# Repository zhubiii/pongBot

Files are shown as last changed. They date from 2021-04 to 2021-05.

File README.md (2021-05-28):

# pongBot
Progress on building a robot that can bounce a ping-pong ball forever...maybe more?

- [Methods](#Methods)
  - [Kinematics](#Kinematics)
  - [Theta offset](#Theta-offset)
  - [ROS](#ROS)
  - [Simulation](#Simulation)
    - [URDF](#URDF)
- [Build Progress](#Build-Progress)
  - [VERSION1](#VERSION1)
    - [Controller-Agent Unit](#Controller-Agent-Unit)
    - [Base](#Base)
    - [Link1](#Link-1)
    - [Link2](#Link-2)
    - [End-Effector](#End-Effector)
  - [VERSION2](#VERSION2)
- [Problems Encountered](#Problems-Encountered!)
- [TODO](#TODO)

# Methods
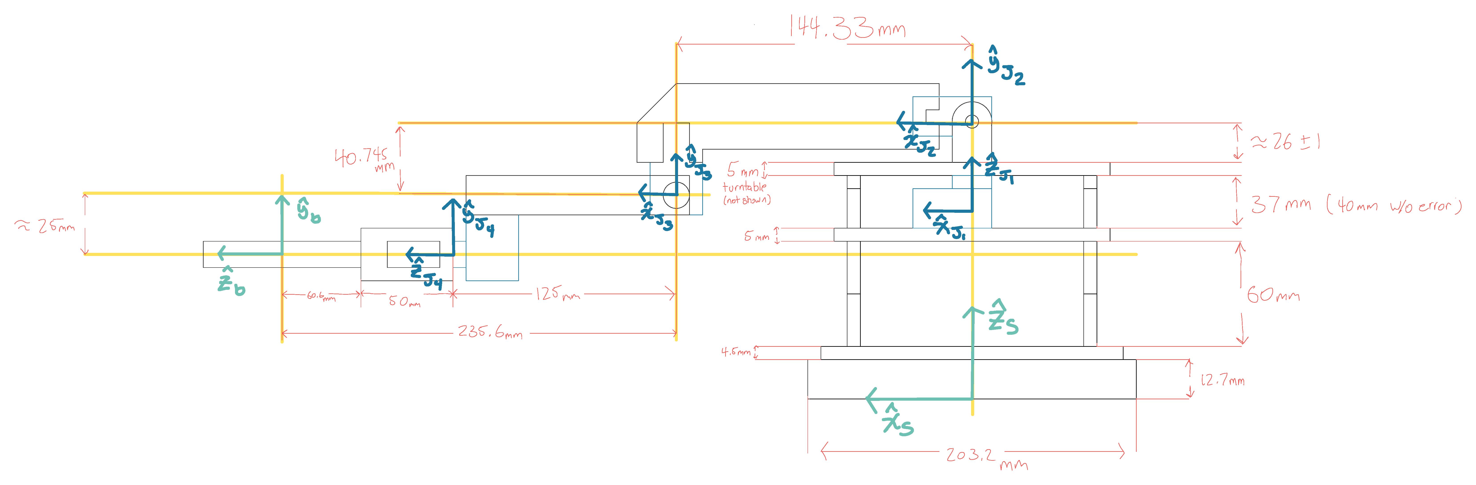
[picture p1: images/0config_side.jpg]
0config_side

## Kinematics
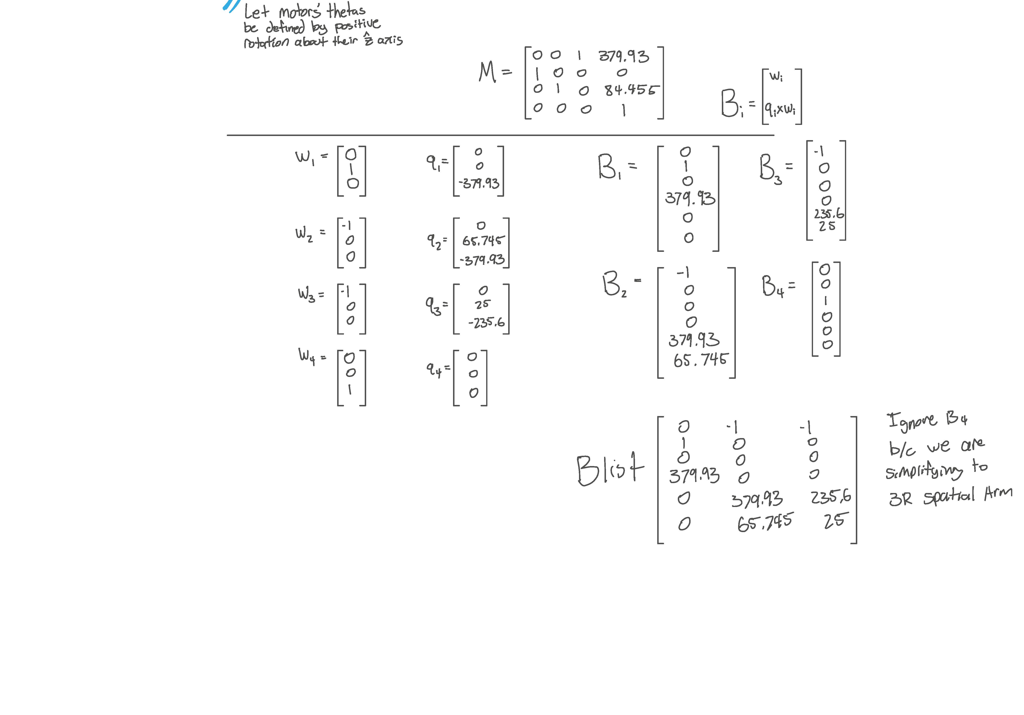
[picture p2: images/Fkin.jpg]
Fkin

## Theta offset
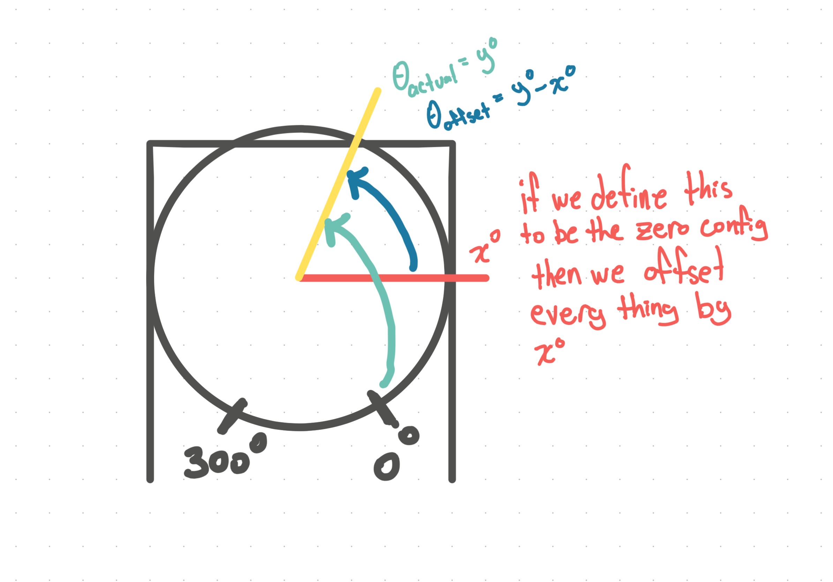
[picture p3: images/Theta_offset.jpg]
Theta offset

## ROS
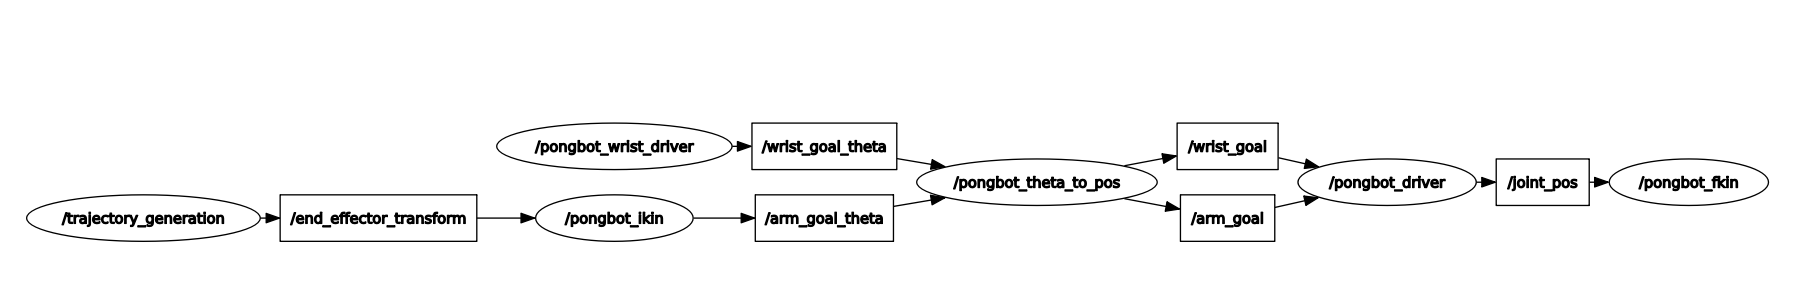
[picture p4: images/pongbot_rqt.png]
Rqt_graph


## Simulation

### URDF
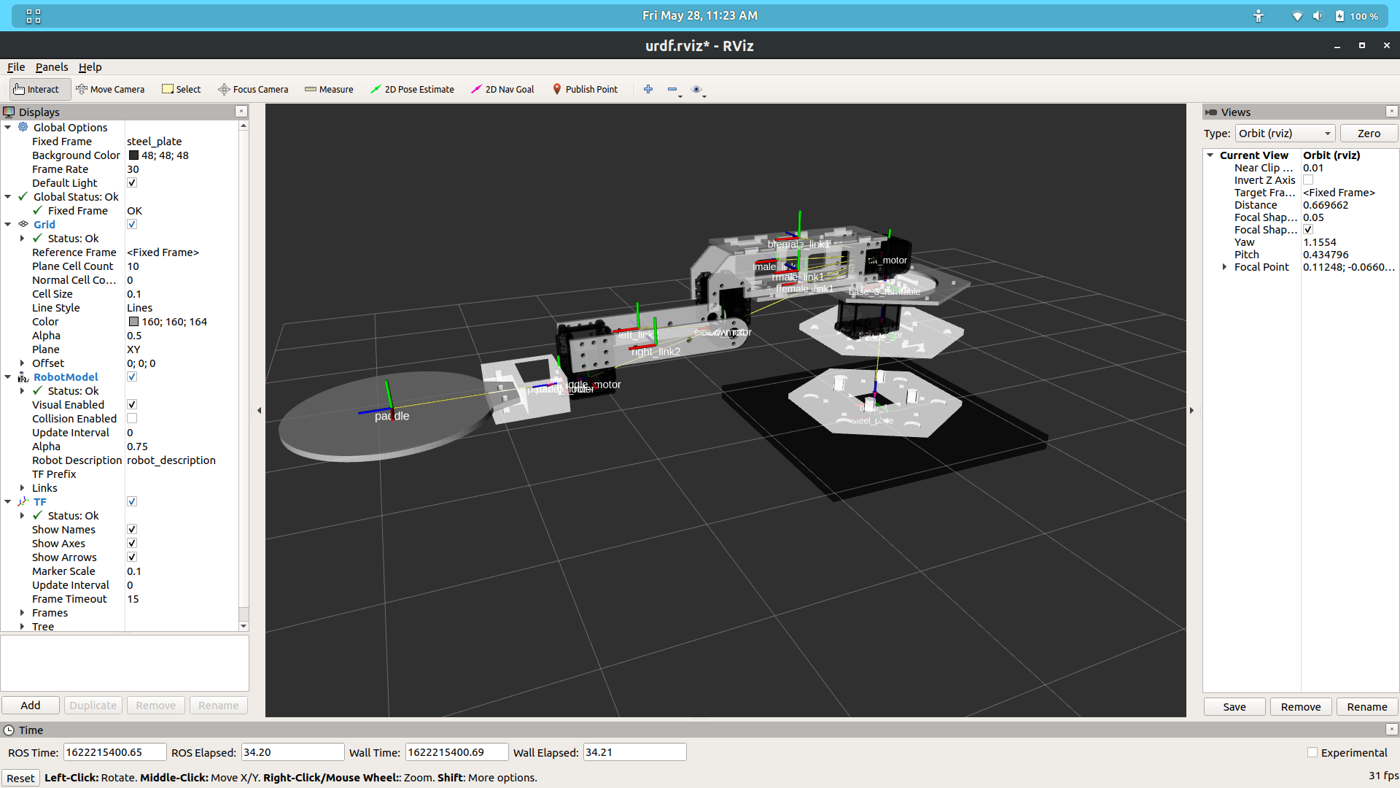
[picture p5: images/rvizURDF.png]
URDF in Rviz


# Build Progress
## VERSION1
### Controller-Agent Unit
- There are two of these units, one is the controller and one is the agent. The agent will always mimic the pan/tilt position of the controller   
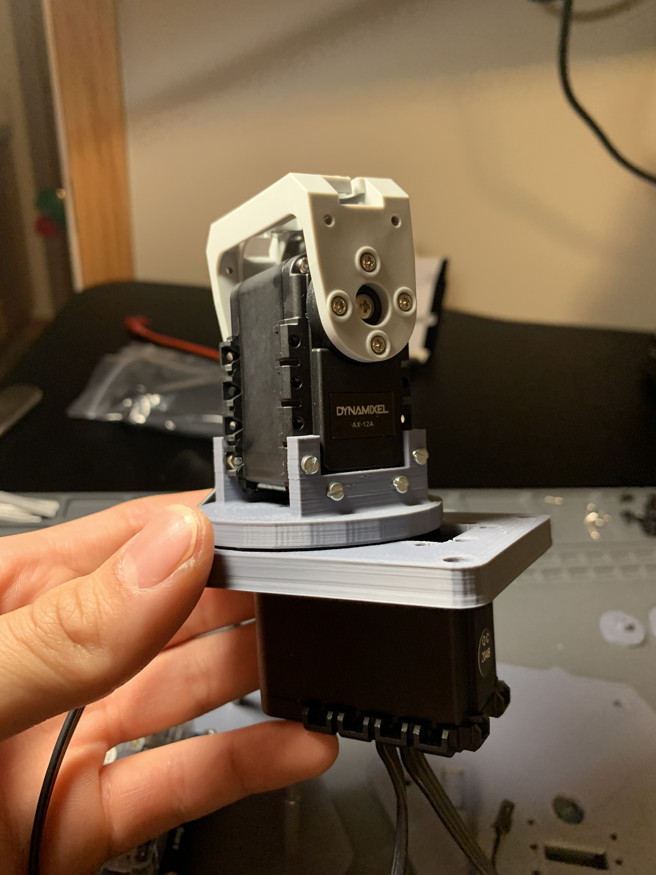
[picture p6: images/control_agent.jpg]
controller_agent


### Base
- There are 3 layers to the base
  - The first layer houses the U2D2 controller/PC interface
  - The second layer holds the pan motor which has the turntable attached to it and a spacer between for level
  - The third layer hodls the tilt motor which is a combination of the turntable and the rim
- Each of the layers are attached by standoffs
- I have plans to attach a steel plate to the bottom of the base such that the arm does not backflip off of a single rotation

. | . | .
:-:|:-:|:-:
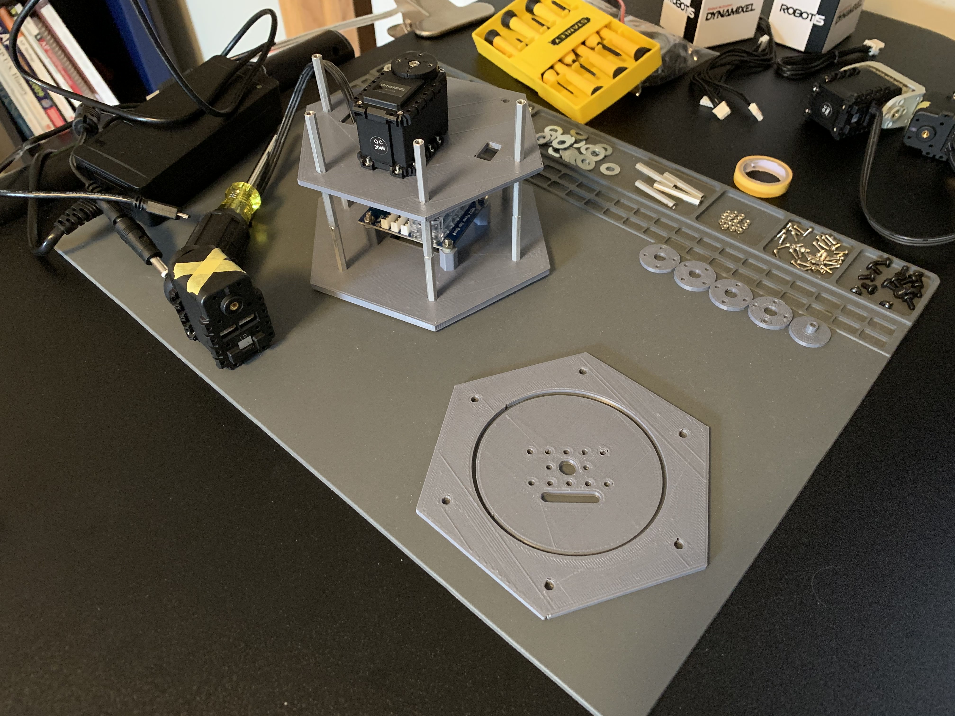
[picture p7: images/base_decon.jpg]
base deconstructed
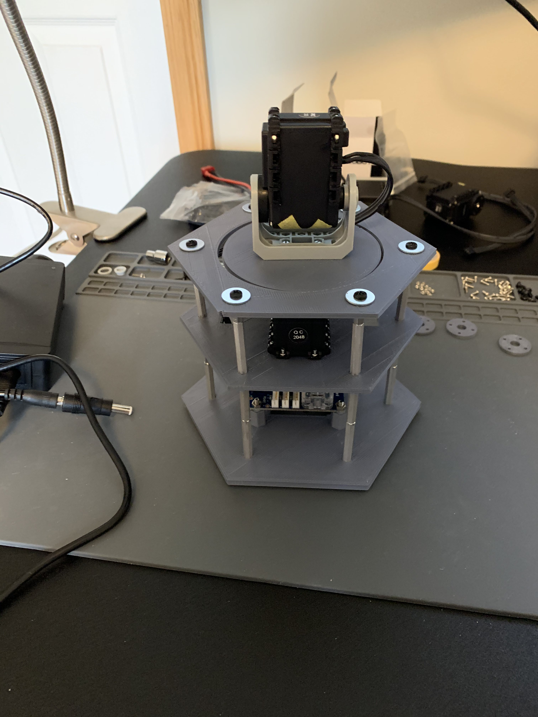
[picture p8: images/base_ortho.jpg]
base ortho view
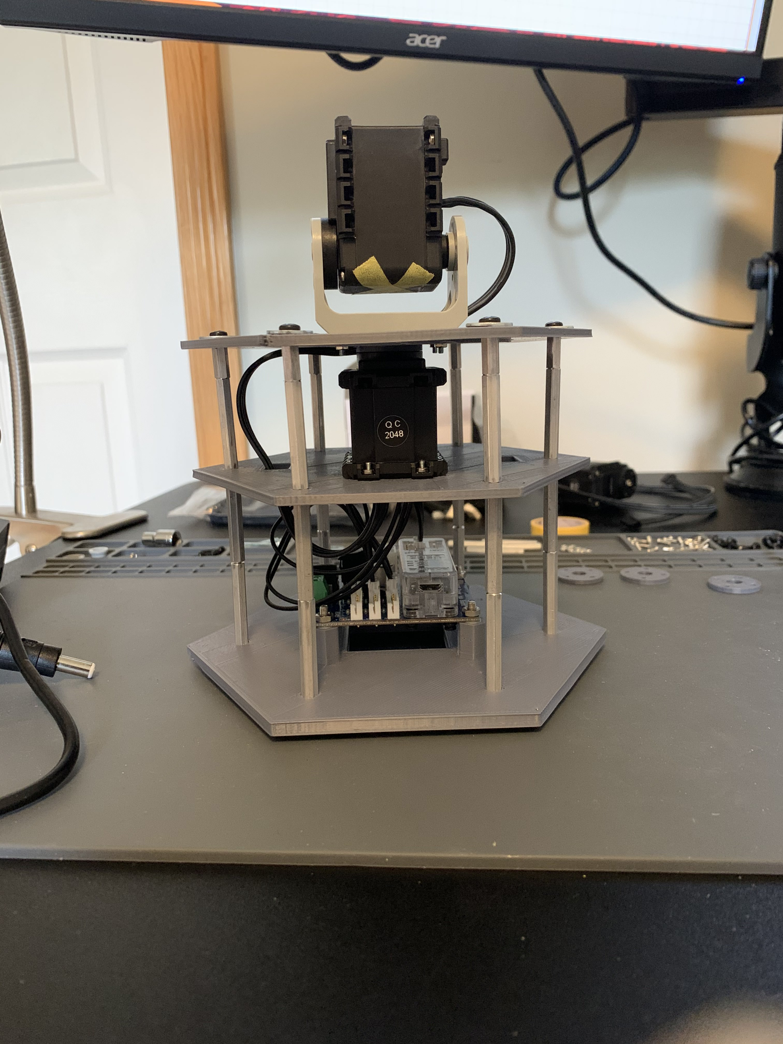
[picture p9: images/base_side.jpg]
base side view
||

### Link 1
- The first link is 4 plates that attach to the tilt motor. The front and back plates are linked by a standoff for support. The end of the link holds the second arm joint.

.|.|.|.
:-:|:-:|:-:|:-:
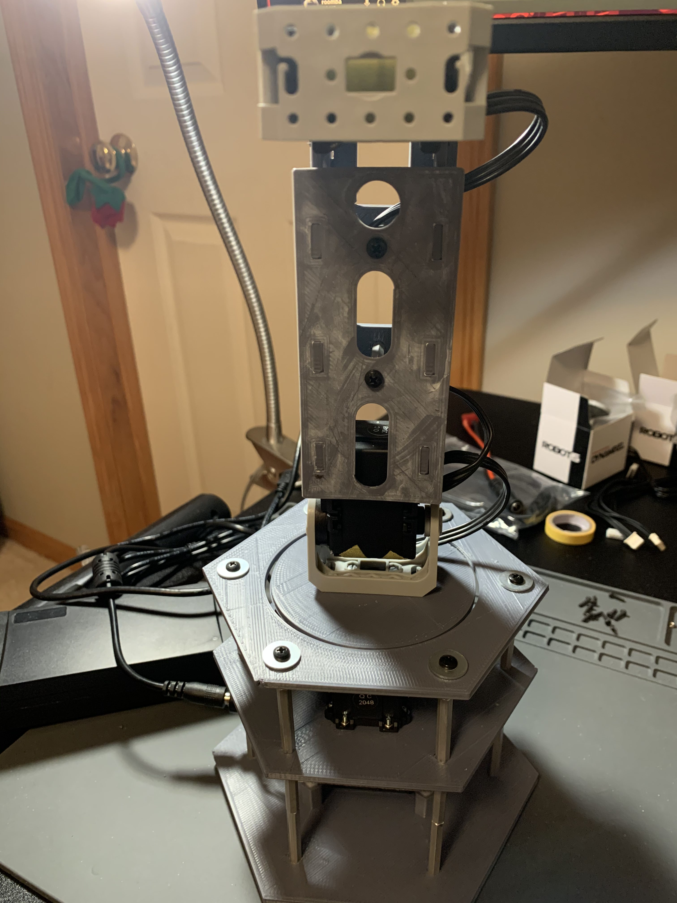
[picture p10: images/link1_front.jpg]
link1 front
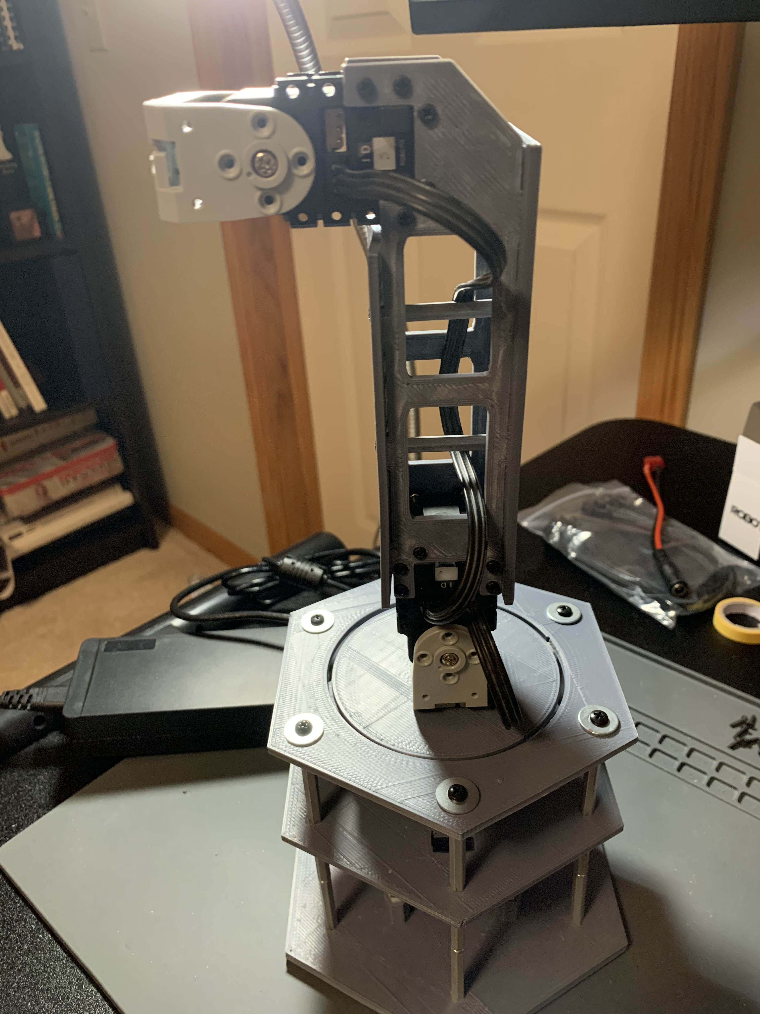
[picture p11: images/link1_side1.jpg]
link side1
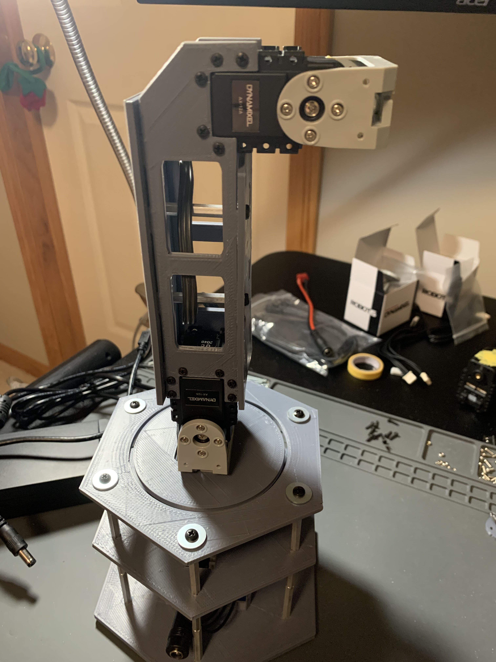
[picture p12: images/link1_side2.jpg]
link_side2
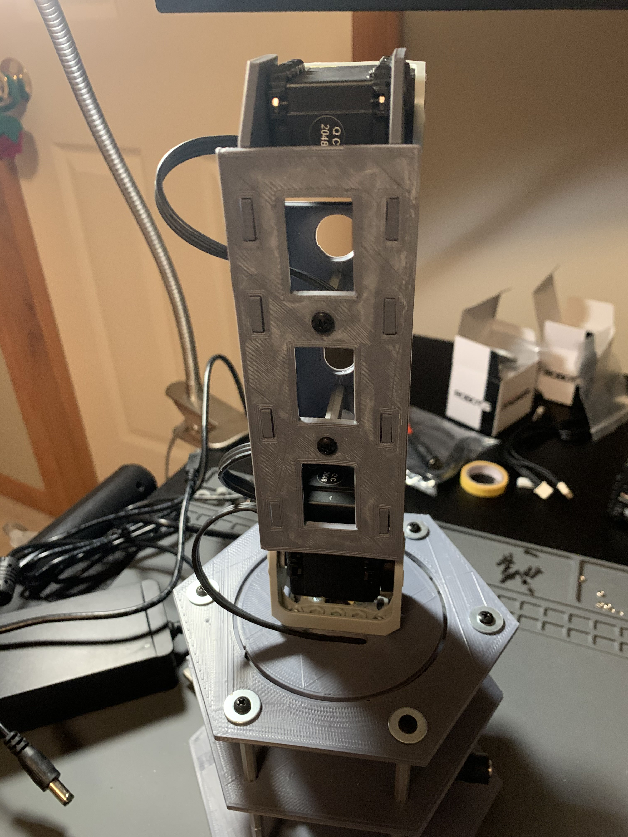
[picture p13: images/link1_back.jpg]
link_back
 |  |  | 

### Link 2
- The second link is a combination of 2 side panels joined by a standoff for support. The end of link2 holds the end effector

.|.|.|.
:-:|:-:|:-:|:-:
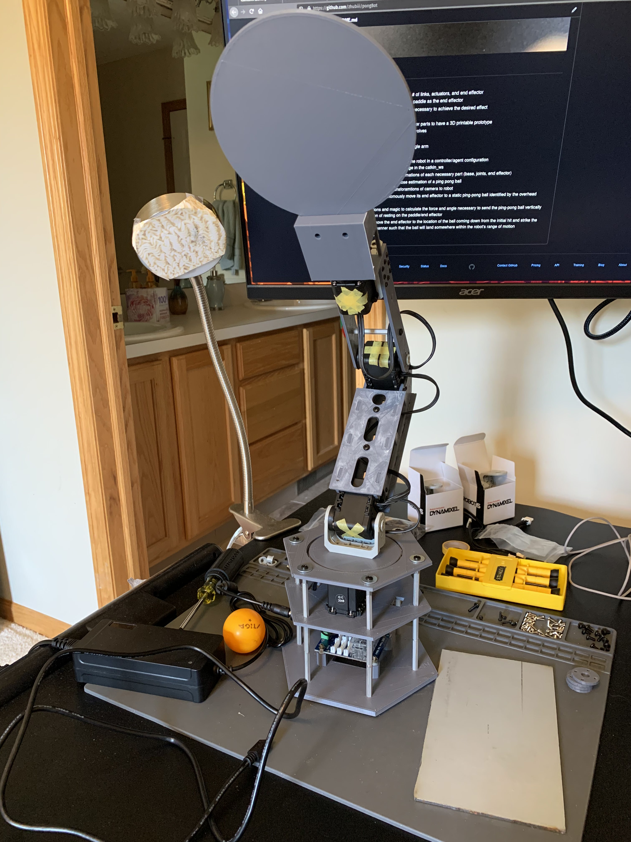
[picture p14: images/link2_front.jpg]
link2 front
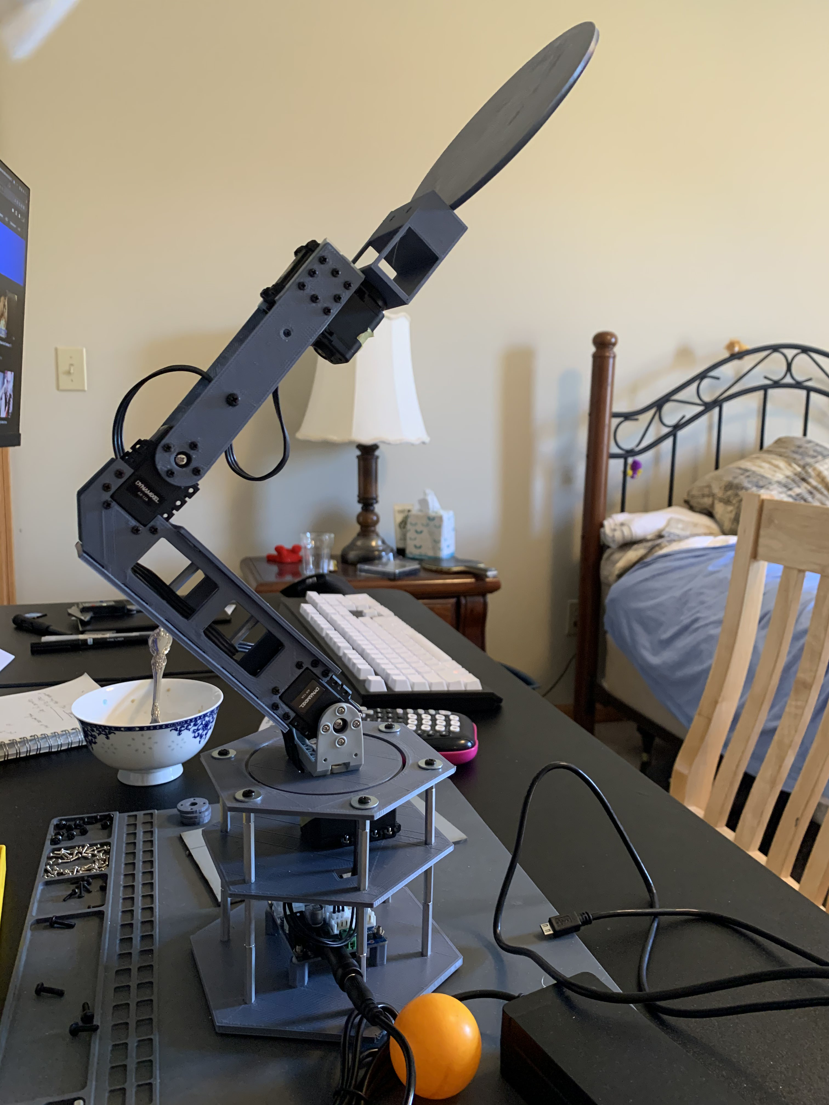
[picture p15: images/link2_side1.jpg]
link1 side1
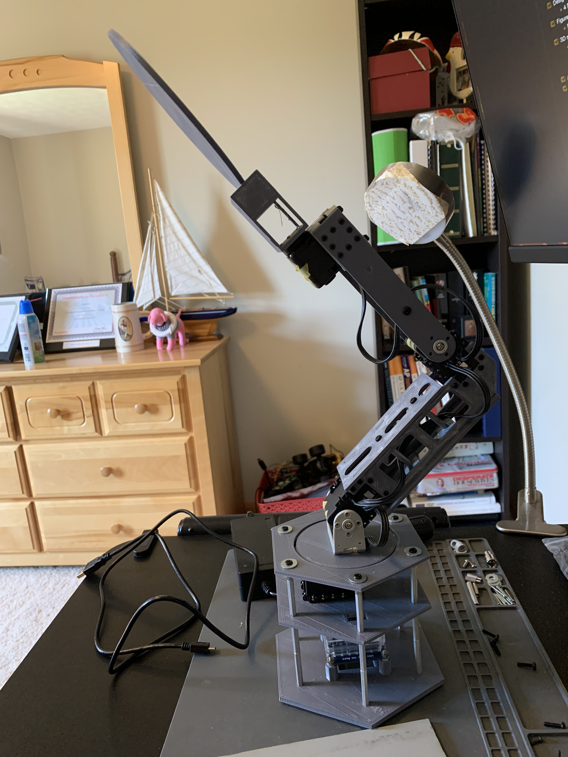
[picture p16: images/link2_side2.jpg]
link2_side2
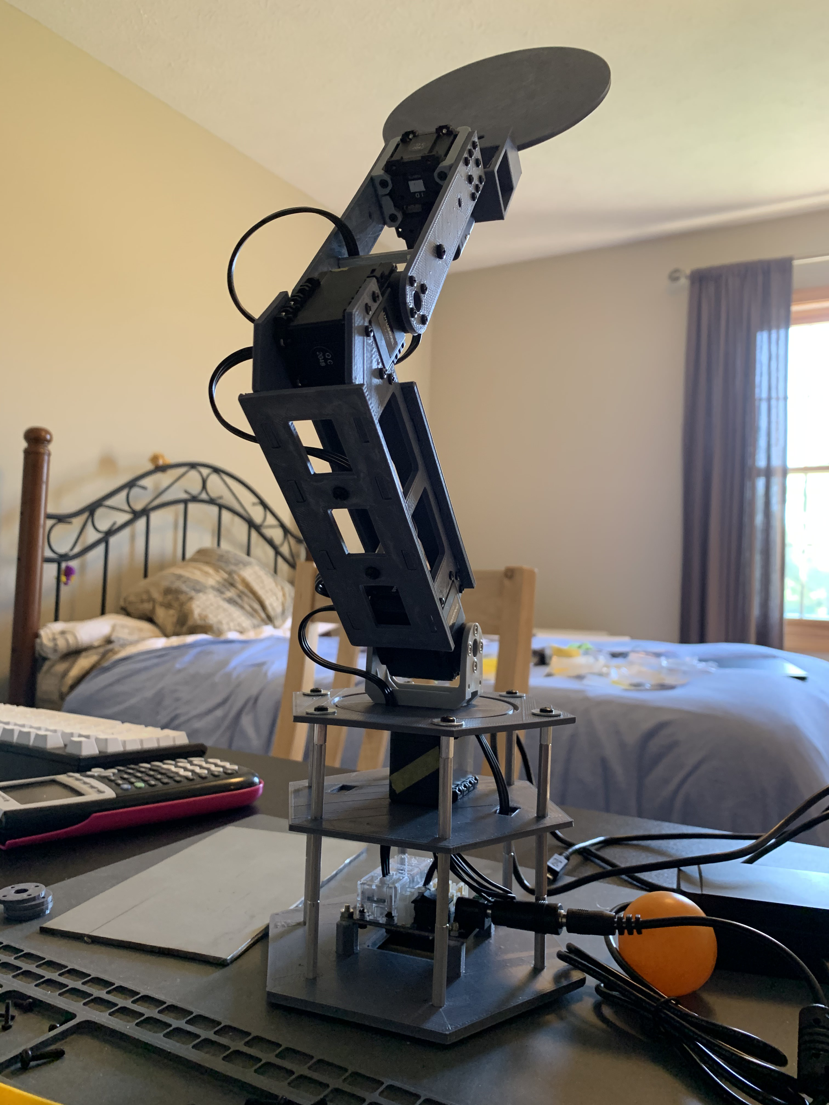
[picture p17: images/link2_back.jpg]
link_back
 |  |  | 

### End Effector
-  The end effector is a two piece 3-D printed paddle that attaches to a motor for angle control

## VERSION2
- The clear parts represents the reprints in PLA. I made them slightly thicker to reduce the wobble problem. In between the 
turntable and base2, I also put support beams. These were intended to have ball bearings on top but frankly I did not have
any on me at the time. I discovered, however, that the plastics are smooth enough to support and slide with minimal frictional resistance
- Lastly I was able to get a half-inch thick steel plate (thanks dad) to bolt the arm's base to. I drilled and tapped holes into it so 
now the arm will not do backflips everytime I attempt to move the end-effector

.|.
:-:|:-:
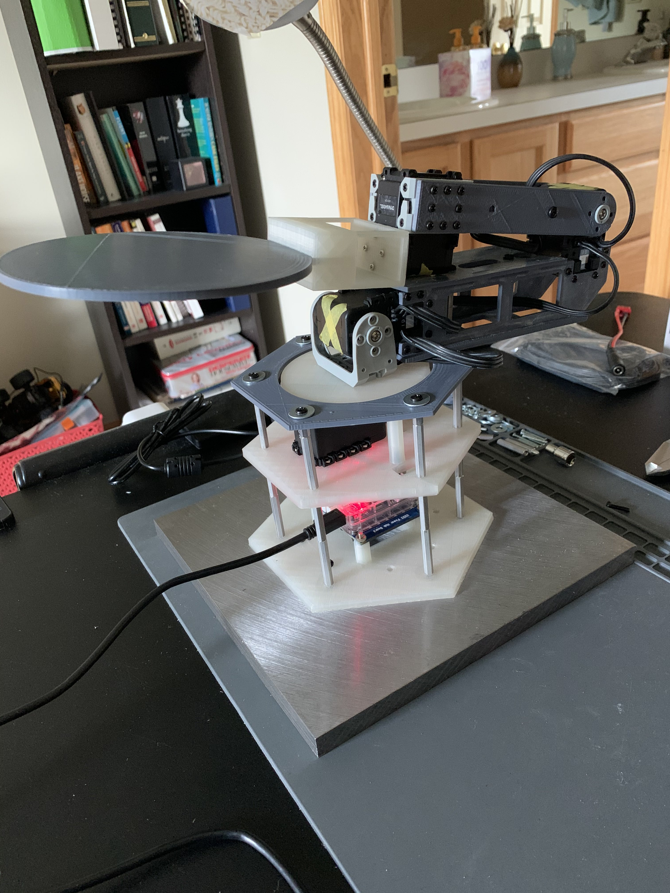
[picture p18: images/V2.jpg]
V2
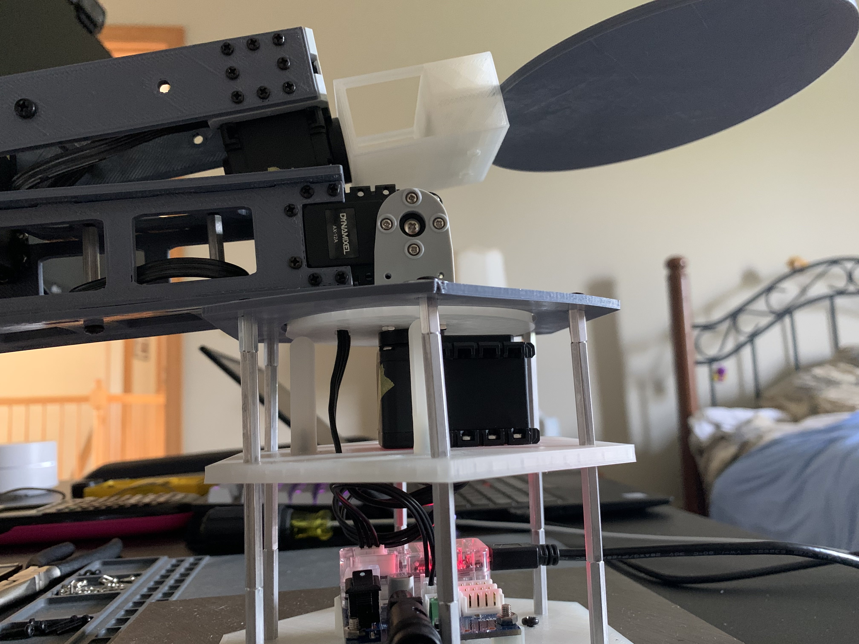
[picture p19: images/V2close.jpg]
V2 close
 | 

# Problems Encountered!
- WOBBLE
  - There is a lot of wobble in the first fully assembled test run. The turntable and second-level base (base2) are the source of a lot of instability in the system. The shaft of the motor is much smaller than the diameter of the turntable which causes wobbling. Additionally, base2 has a "trampoline" effect
  - Going to double the thickness of base2 and the turntable, and also look into designing ball-bearing support beams for the table. Will likely shift from ABS to PLA filament for these because PLA has higher rigidity 
- LIMITED DOF
  - There is not 6DOF which makes trajectory generation difficult. We are unable to easily define the workspace of the arm and therefore cannot pick arbitrary configurations for the arm to follow. This motivates the investigation into using Reinforcement Learning to allow complex behavior
  - Will spend time getting the robot in simulation to use as a testbed for AI controllers

# TODO
- [x] Find cool project
- [x] Design crude sketch, specifying DOF, # of links, actuators, and end effector
  - 4 DOF, 2 links, 4 actuators, and a paddle as the end effector
- [x] Figure out and purchase the actuators necessary to achieve the desired effect
  - Dynamixel AX-12a
- [x] 3D model necessary links, base, and other parts to have a 3D printable prototype
  - Will have redesigns as the project evolves
  - First was a simple pan/tilt setup
  - Next is to combine motors into a single arm
- [x] Assemble and wire parts together
- [x] Write driver code to be able to control the robot in a controller/agent configuration
  -  See the "controller_agent" package in the catkin_ws
- [x] Combine all motors into a single robot arm
  - [x] DETOUR: Redesign turntable and base2 in PLA to fix wobble. Also design ball-bearing support beams
- [x] Figure out coordinate frame transformations of each necessary part (base, joints, end effector)
- [ ] Get robot in simulation
  - [x] URDF
  - [x] Rviz
  - [ ] Gazebo
- [ ] Test Reinforcement Learning controls on simulation
- [ ] Write code to do a "show floor" run of all of the robots capabilities
- [ ] Use OpenCV to identify and get pose estimation of a ping pong ball
- [ ] Figure out coordinate frame transforamtions of camera to robot
- [ ] Be able to have robot autonomously move its end effector to a static ping-pong ball identified by the overhead camera
- [ ] Use physics equations and magic to calculate the force and angle necessary to send the ping-pong ball vertically from a static position of resting on the paddle/end effector
- [ ] Use said magic to move the end effector to the location of the ball coming down from the initial hit and strike the ball in a controlled manner such that the ball will land somewhere within the robot's range of motion
- [ ] Repeat previous step

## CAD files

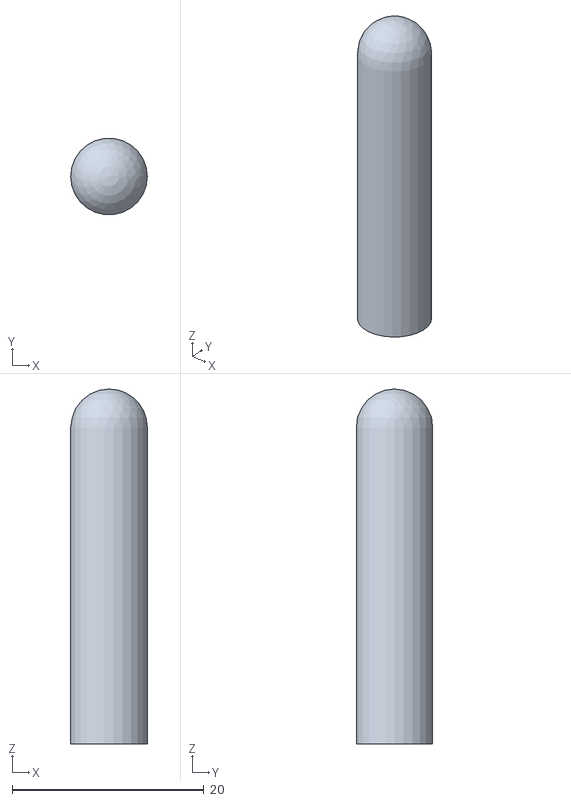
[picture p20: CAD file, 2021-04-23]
catkin_ws/src/pongbot/meshes/base/turntable_support-Fusion.stl
8.00 x 7.94 x 37.0

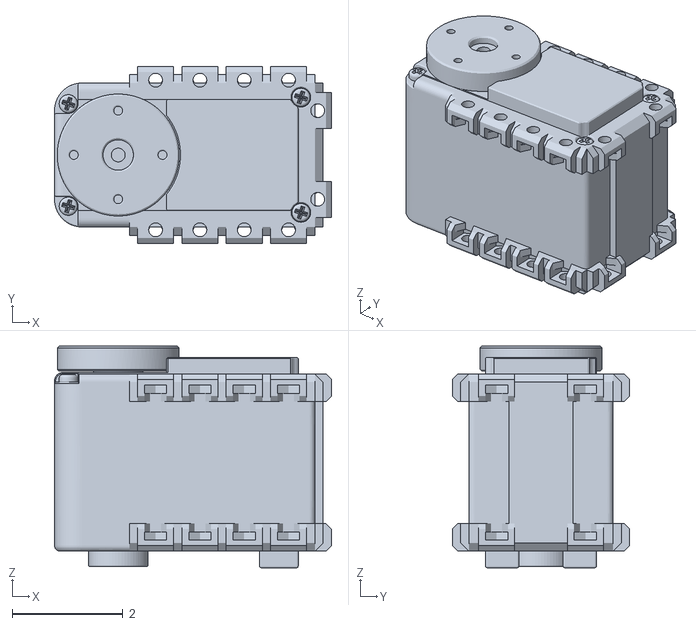
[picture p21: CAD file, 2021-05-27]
catkin_ws/src/pongbot/meshes/dxl.stl
5.00 x 3.20 x 4.00

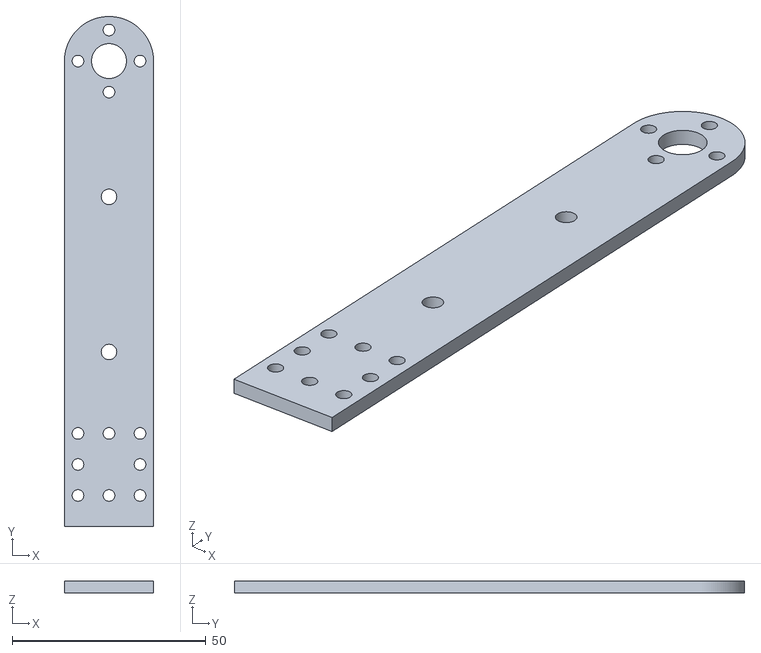
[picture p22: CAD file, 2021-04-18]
catkin_ws/src/pongbot/meshes/links/Link2_sidepanel-Body.stl
23.0 x 131.5 x 3.00

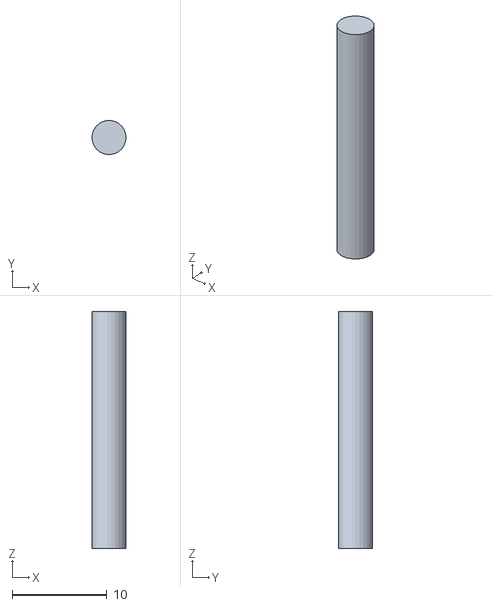
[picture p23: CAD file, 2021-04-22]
catkin_ws/src/pongbot/meshes/paddle/stop_rod-Body.stl
3.60 x 3.57 x 25.0

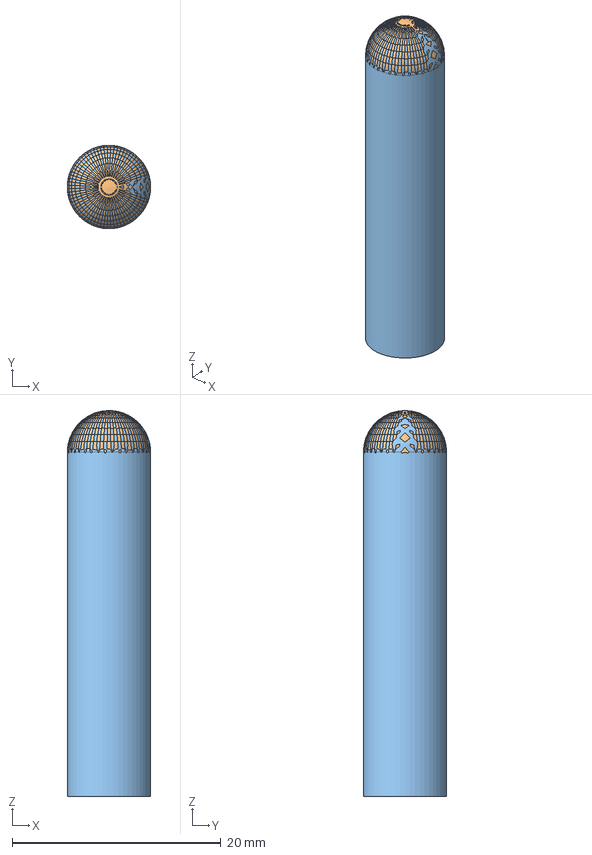
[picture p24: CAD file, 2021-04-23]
models/CAD/base/turntable_support.FCStd
7.99 x 8.00 x 37.0 mm

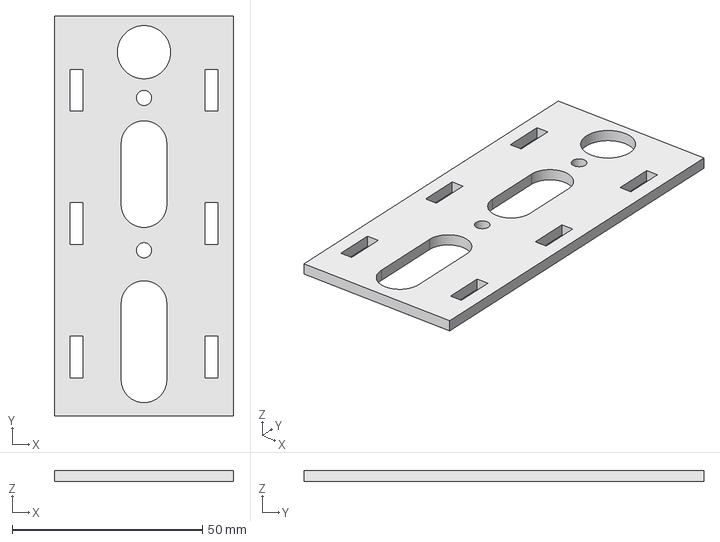
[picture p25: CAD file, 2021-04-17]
models/CAD/Female_Link1_frontPanel.FCStd
47.0 x 105.0 x 3.00 mm

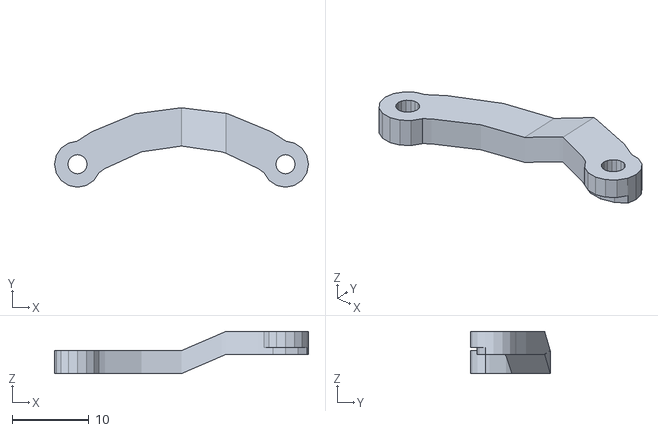
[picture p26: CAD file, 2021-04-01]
models/Robot_Arm_For_AX-12A_Dynamixel_Actuators/the_crawer_lever.stl
33.1 x 10.4 x 5.50

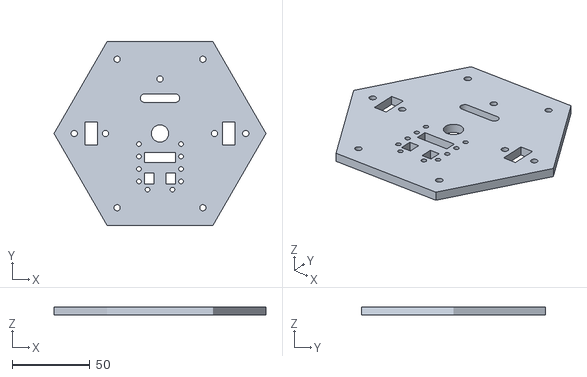
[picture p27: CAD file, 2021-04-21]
catkin_ws/src/pongbot/meshes/base/base2-Body.stl
136.0 x 117.8 x 5.00

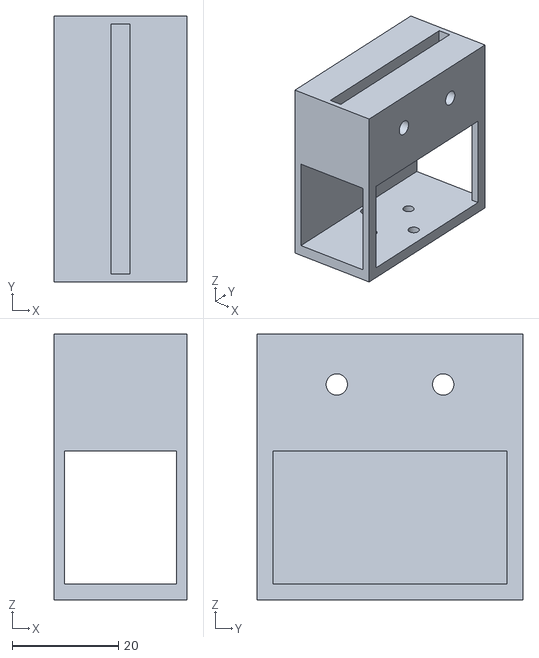
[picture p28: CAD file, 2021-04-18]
catkin_ws/src/pongbot/meshes/paddle/paddle_holder-Body.stl
25.0 x 50.0 x 50.0

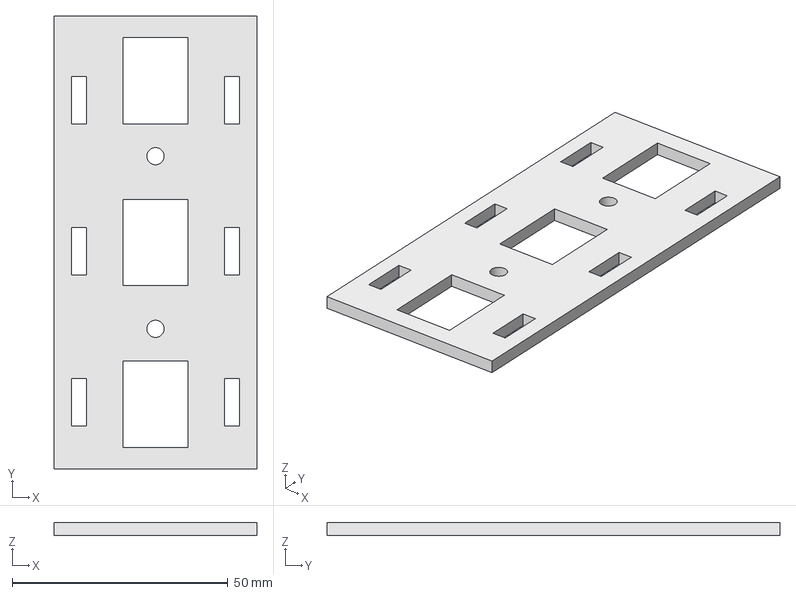
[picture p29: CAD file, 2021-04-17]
models/CAD/links/Female_Link1_frontPanel.FCStd
47.0 x 105.0 x 3.00 mm

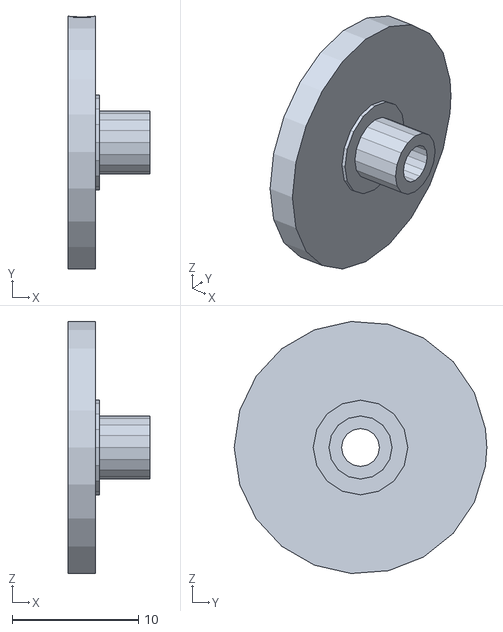
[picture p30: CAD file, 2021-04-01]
models/Robot_Arm_For_AX-12A_Dynamixel_Actuators/servo_hinge_flange.stl
6.50 x 20.0 x 19.9

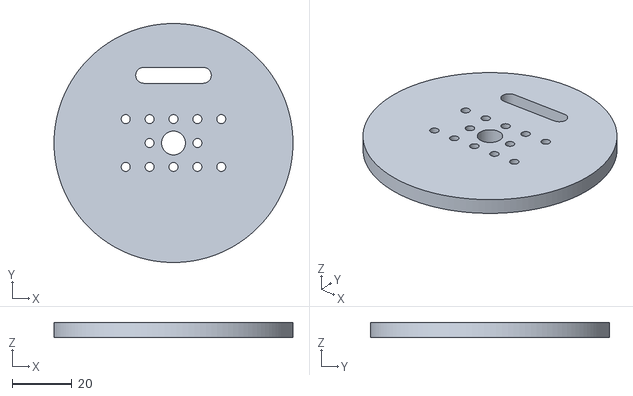
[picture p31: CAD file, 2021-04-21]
catkin_ws/src/pongbot/meshes/base/base3_turntable-Body.stl
80.0 x 80.0 x 5.00

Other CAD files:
models/CAD/links/Link2_sidepanel.FCStd
models/CAD/paddle/stop_rod.FCStd
catkin_ws/src/pongbot/meshes/links/Female_Link1_frontPanel-Body.stl
models/CAD/AX-12A.dwg
models/CAD/base/base2.FCStd
models/CAD/paddle/paddle_holder.FCStd
catkin_ws/src/pongbot/meshes/base/base1-Body.stl
catkin_ws/src/pongbot/meshes/base/base3_rim-Body.stl
catkin_ws/src/pongbot/meshes/base/turntable_spacer-Body.stl
catkin_ws/src/pongbot/meshes/links/Female_Link1_backPanel-Body.stl
catkin_ws/src/pongbot/meshes/links/Male_Link1_Panel-Body.stl
catkin_ws/src/pongbot/meshes/paddle/paddle-Body.stl
models/CAD/Link_prototype.FCStd
models/CAD/Male_Link_Connector.FCStd
models/CAD/base/base1.FCStd
models/CAD/base/base3_rim.FCStd
models/CAD/base/base3_turntable.FCStd
models/CAD/base/turntable_spacer.FCStd
models/CAD/links/Female_Link1_backPanel.FCStd
models/CAD/links/Male_Link1_Panel.FCStd
models/CAD/paddle/paddle.FCStd
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

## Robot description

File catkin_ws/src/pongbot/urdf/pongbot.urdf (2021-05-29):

<?xml version="1.0"?>
<robot name="pongbot">

    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
    <link name="dummy_root">
        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
    </link>

    <link name="steel_plate">
        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
        <inertial>
            <mass value="4.211"/>
            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
        </inertial>
    </link>

    <joint name="dummy_to_steel" type="fixed">
        <parent link="dummy_root"/>
        <child link="steel_plate"/>
        <origin xyz="0 0 0" />
    </joint>

    <link name="base_1">
        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
        <inertial>
            <mass value="0.047"/>
            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
        </inertial>
    </link>

    <joint name="steel_to_base1" type="fixed">
        <parent link="steel_plate"/>
        <child link="base_1"/>
        <origin xyz="0 0 .0127" />
    </joint>

    <link name="base_2">
        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
        <inertial>
            <mass value="0.041"/>
            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
        </inertial>
    </link>

    <joint name="base1_to_base2" type="fixed">
        <parent link="base_1"/>
        <child link="base_2"/>
        <origin xyz="0 0 .0645" />
    </joint>

    <link name="pan_motor">
        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
        <inertial>
            <mass value="0.0535"/>
            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
        </inertial>
    </link>

    <joint name="steel_to_pan_motor" type="fixed">
        <parent link="steel_plate"/>
        <child link="pan_motor"/>
        <origin xyz="0 0 .080" />
    </joint>

    <link name="base_3_rim">
        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
        <inertial>
            <mass value="0.016"/>
            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
        </inertial>
    </link>

    <joint name="base2_to_base3_rim" type="fixed">
        <parent link="base_2"/>
        <child link="base_3_rim"/>
        <origin xyz="0 0 .042" />
    </joint>

    <link name="base_3_turntable">
        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
        <inertial>
            <mass value="0.017"/>
            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
        </inertial>
    </link>

    <joint name="pan_joint" type="revolute">
        <parent link="pan_motor"/>
        <child link="base_3_turntable"/>
        <origin xyz="0 0 0.037" />
        <limit effort="1.5" lower="-2.61799" upper="2.61799" velocity="0.5"/>
        <axis xyz="0 0 1"/>
    </joint>

    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

    <link name="tilt_motor">
        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
        <inertial>
            <mass value="0.0535"/>
            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
        </inertial>
    </link>

    <joint name="tilt_joint" type="revolute">
        <parent link="base_3_turntable"/>
        <child link="tilt_motor"/>
        <origin rpy="1.57075 0 0 " xyz="0 0 0.026" />
        <limit effort="1.5" lower="0" upper="3.14159" velocity="0.5"/>
        <axis xyz="0 0 1"/>
    </joint>

    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

    <link name="rmale_link1">
        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
        <inertial>
            <mass value="0.007"/>
            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
        </inertial>
    </link>

    <joint name="tilt_to_right_link1" type="fixed">
        <parent link="tilt_motor"/>
        <child link="rmale_link1"/>
        <origin rpy="0 0 0" xyz="0.091 0 -0.017" />
    </joint>

    <link name="lmale_link1">
        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
        <inertial>
            <mass value="0.007"/>
            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
        </inertial>
    </link>

    <joint name="tilt_to_left_link1" type="fixed">
        <parent link="tilt_motor"/>
        <child link="lmale_link1"/>
        <origin rpy="0 0 0" xyz="0.091 0 0.017" />
    </joint>

    <link name="bfemale_link1">
        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
        <inertial>
            <mass value="0.011"/>
            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
        </inertial>
    </link>

    <joint name="tilt_to_back_link1" type="fixed">
        <parent link="tilt_motor"/>
        <child link="bfemale_link1"/>
        <origin rpy="0 0 0" xyz="0.082 0.02 0" />
    </joint>

    <link name="ffemale_link1">
        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
        <inertial>
            <mass value="0.010"/>
            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
        </inertial>
    </link>

    <joint name="tilt_to_front_link1" type="fixed">
        <parent link="tilt_motor"/>
        <child link="ffemale_link1"/>
        <origin rpy="0 0 0" xyz="0.075 -0.015 0" />
    </joint>

    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

    <link name="elbow_motor">
        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
        <inertial>
            <mass value="0.0535"/>
            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
        </inertial>
    </link>

    <joint name="tilt_to_elbow_motor" type="fixed">
        <parent link="tilt_motor"/>
        <child link="elbow_motor"/>
        <origin rpy="0 0 0 " xyz="0.14433 -0.040745 0" />
    </joint>

    <link name="elbow_rot">
        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
        <inertial>
            <mass value="0"/>
            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
        </inertial>
    </link>

    <joint name="elbow_joint" type="revolute">
        <parent link="elbow_motor"/>
        <child link="elbow_rot"/>
        <origin rpy="0 0 0 " xyz="0 0 0" />
        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
        <limit effort="1.5" lower="-2.96705" upper="0" velocity="0.5"/>
        <axis xyz="0 0 1"/>
    </joint>

    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

    <link name="left_link2">
        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
        <inertial>
            <mass value="0.007"/>
            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
        </inertial>
    </link>

    <joint name="elbow_to_left_link2" type="fixed">
        <parent link="elbow_rot"/>
        <child link="left_link2"/>
        <origin rpy="0 0 0" xyz="0.06 0 .02" />
    </joint>

    <link name="right_link2">
        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
        <inertial>
            <mass value="0.007"/>
            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
        </inertial>
    </link>

    <joint name="elbow_to_right_link2" type="fixed">
        <parent link="elbow_rot"/>
        <child link="right_link2"/>
        <origin rpy="0 0 0" xyz="0.06 0 -.02" />
    </joint>

    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

    <link name="paddle_motor">
        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
        <inertial>
            <mass value="0.0535"/>
            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
        </inertial>
    </link>

    <joint name="elbow_to_paddle_motor" type="fixed">
        <parent link="elbow_rot"/>
        <child link="paddle_motor"/>
        <origin rpy="0 1.57075 0 " xyz="0.105 -0.025 0" />
    </joint>

    <link name="paddle_rot">
        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
        <inertial>
            <mass value="0"/>
            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
        </inertial>
    </link>

    <joint name="paddle_joint" type="continuous">
        <parent link="paddle_motor"/>
        <child link="paddle_rot"/>
        <origin rpy="0 0 0 " xyz="0 0 0.02" />
        <axis xyz="0 0 1"/>
        <limit effort="1.5" velocity="1.0"/>
    </joint>

    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

    <link name="paddle_holder">
        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
        <inertial>
            <mass value="0.021"/>
            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
        </inertial>
    </link>

    <joint name="paddle_motor_to_paddle_holder" type="fixed">
        <parent link="paddle_rot"/>
        <child link="paddle_holder"/>
        <origin rpy="0 0 0 " xyz="0 0 0" />
    </joint>

    <link name="paddle">
        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
        <inertial>
            <mass value="0.037"/>
            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
        </inertial>
    </link>

    <joint name="paddle_rot_to_paddle" type="fixed">
        <parent link="paddle_rot"/>
        <child link="paddle"/>
        <origin rpy="0 0 0 " xyz="0 0 0.1106" />
    </joint>

    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
</robot>

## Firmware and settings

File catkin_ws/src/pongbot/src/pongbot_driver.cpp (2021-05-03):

#include <ros/ros.h>
#include <ros/console.h>
#include <dynamixel_sdk.h>

#include <stdlib.h>
#include <stdio.h>
#include <string>

#include <pongbot/JointGoal.h>
#include <pongbot/WristGoal.h>

#define TORQUE_ENABLE   1
#define TORQUE_DISABLE  0
#define NUM_JOINTS  4

uint32_t joint_pos[4];
// init values with zero config
uint32_t goal_pos[3] = {512, 750, 819};
uint32_t wrist_goal = 512;

// Get all parameters from the yaml config file
std::string DEVICENAME;
int DXL_MINIMUM_POSITION_VALUE, DXL_MAXIMUM_POSITION_VALUE, BAUDRATE;
float PROTOCOL_VERSION;
int ADDR_TORQUE_ENABLE, ADDR_GOAL_POSITION, ADDR_PRESENT_POSITION, ADDR_SPEED, ADDR_CW_COMPLIANCE_SLOPE, ADDR_CCW_COMPLIANCE_SLOPE;
int JOINT_PAN_ID, JOINT_TILT_ID, JOINT_ELBOW_ID, JOINT_PADDLE_ID;
int JOINT_PAN_SPEED, JOINT_TILT_SPEED, JOINT_ELBOW_SPEED, JOINT_PADDLE_SPEED;
int JOINT_PAN_CCW_COMPLIANCE_SLOPE, JOINT_TILT_CCW_COMPLIANCE_SLOPE, JOINT_ELBOW_CCW_COMPLIANCE_SLOPE, JOINT_PADDLE_CCW_COMPLIANCE_SLOPE;
int JOINT_PAN_CW_COMPLIANCE_SLOPE, JOINT_TILT_CW_COMPLIANCE_SLOPE, JOINT_ELBOW_CW_COMPLIANCE_SLOPE, JOINT_PADDLE_CW_COMPLIANCE_SLOPE;

// Function prototypes
void checkCommResult(int dxl_comm_result, dynamixel::PacketHandler *packetHandler, uint8_t dxl_error);
void updateGoalArm(const pongbot::JointGoal::ConstPtr& msg);
void updateGoalWrist(const pongbot::WristGoal::ConstPtr& msg);
void getJointPos(dynamixel::PacketHandler* packetHandler, dynamixel::PortHandler* portHandler, int dxl_comm_result, uint8_t dxl_error);
void setJointPos(dynamixel::PacketHandler* packetHandler, dynamixel::PortHandler* portHandler, int dxl_comm_result, uint8_t dxl_error);

int main(int argc, char** argv)
{
    // init node
    ros::init(argc, argv, "pongbot_driver");

    ros::NodeHandle n;


    n.getParam("usb_port", DEVICENAME);
    n.getParam("dxl_minimum_position_value", DXL_MINIMUM_POSITION_VALUE);
    n.getParam("dxl_maximum_position_value", DXL_MAXIMUM_POSITION_VALUE);
    n.getParam("dxl_baud_rate", BAUDRATE);
    n.getParam("protocol_version", PROTOCOL_VERSION);
    n.getParam("addr_torque_enable", ADDR_TORQUE_ENABLE);
    n.getParam("addr_goal_position", ADDR_GOAL_POSITION);
    n.getParam("addr_present_position", ADDR_PRESENT_POSITION);
    n.getParam("addr_speed", ADDR_SPEED);
    n.getParam("addr_cw_compliance_slope", ADDR_CW_COMPLIANCE_SLOPE);
    n.getParam("addr_ccw_compliance_slope", ADDR_CCW_COMPLIANCE_SLOPE);
    n.getParam("joint_pan/ID", JOINT_PAN_ID);
    n.getParam("joint_tilt/ID", JOINT_TILT_ID);
    n.getParam("joint_elbow/ID", JOINT_ELBOW_ID);
    n.getParam("joint_paddle/ID", JOINT_PADDLE_ID);
    n.getParam("joint_pan/speed", JOINT_PAN_SPEED);
    n.getParam("joint_tilt/speed", JOINT_TILT_SPEED);
    n.getParam("joint_elbow/speed", JOINT_ELBOW_SPEED);
    n.getParam("joint_paddle/speed", JOINT_PADDLE_SPEED);
    n.getParam("joint_pan/ccw_compliance_slope", JOINT_PAN_CCW_COMPLIANCE_SLOPE);
    n.getParam("joint_tilt/ccw_compliance_slope", JOINT_TILT_CCW_COMPLIANCE_SLOPE);
    n.getParam("joint_elbow/ccw_compliance_slope", JOINT_ELBOW_CCW_COMPLIANCE_SLOPE);
    n.getParam("joint_paddle/ccw_compliance_slope", JOINT_PADDLE_CCW_COMPLIANCE_SLOPE);
    n.getParam("joint_pan/cw_compliance_slope", JOINT_PAN_CW_COMPLIANCE_SLOPE);
    n.getParam("joint_tilt/cw_compliance_slope", JOINT_TILT_CW_COMPLIANCE_SLOPE);
    n.getParam("joint_elbow/cw_compliance_slope", JOINT_ELBOW_CW_COMPLIANCE_SLOPE);
    n.getParam("joint_paddle/cw_compliance_slope", JOINT_PADDLE_CW_COMPLIANCE_SLOPE);

    // Initialize PortHandler instance
    // Set the port path
    // Get methods and members of PortHandlerLinux or PortHandlerWindows
    dynamixel::PortHandler *portHandler = dynamixel::PortHandler::getPortHandler(DEVICENAME.c_str());

    // Initialize PacketHandler instance
    // Set the protocol version
    // Get methods and members of Protocol1PacketHandler or Protocol2PacketHandler
    dynamixel::PacketHandler *packetHandler = dynamixel::PacketHandler::getPacketHandler(PROTOCOL_VERSION);

    int dxl_comm_result = COMM_TX_FAIL;             // Communication result

    uint8_t dxl_error = 0;                          // Dynamixel error

    // Open port
    if (portHandler->openPort())
    {
        ROS_INFO("Succeeded to open the port!\n");
    }
    else
    {
        ROS_ERROR("Failed to open the port!\n");
        return 0;
    }

    // Set port baudrate
    if (portHandler->setBaudRate(BAUDRATE))
    {
        ROS_INFO("Succeeded to change the baudrate!\n");
    }
    else
    {
        ROS_ERROR("Failed to change the baudrate!\n");
        return 0;
    }

    // initialize and connect to each motor
    dxl_comm_result = packetHandler->write1ByteTxRx(portHandler, JOINT_PAN_ID, ADDR_TORQUE_ENABLE, TORQUE_ENABLE, &dxl_error);
    checkCommResult(dxl_comm_result, packetHandler, dxl_error);

    dxl_comm_result = packetHandler->write1ByteTxRx(portHandler, JOINT_TILT_ID, ADDR_TORQUE_ENABLE, TORQUE_ENABLE, &dxl_error);
    checkCommResult(dxl_comm_result, packetHandler, dxl_error);

    dxl_comm_result = packetHandler->write1ByteTxRx(portHandler, JOINT_ELBOW_ID, ADDR_TORQUE_ENABLE, TORQUE_ENABLE, &dxl_error);
    checkCommResult(dxl_comm_result, packetHandler, dxl_error);

    dxl_comm_result = packetHandler->write1ByteTxRx(portHandler, JOINT_PADDLE_ID, ADDR_TORQUE_ENABLE, TORQUE_ENABLE, &dxl_error);
    checkCommResult(dxl_comm_result, packetHandler, dxl_error);

    ROS_INFO("All motors connected successfully \n");

    // Change operating speed of motors
    dxl_comm_result = packetHandler->write2ByteTxRx(portHandler, JOINT_PAN_ID, ADDR_SPEED, JOINT_PAN_SPEED, &dxl_error);
    checkCommResult(dxl_comm_result, packetHandler, dxl_error);

    dxl_comm_result = packetHandler->write2ByteTxRx(portHandler, JOINT_TILT_ID, ADDR_SPEED, JOINT_TILT_SPEED, &dxl_error);
    checkCommResult(dxl_comm_result, packetHandler, dxl_error);

    dxl_comm_result = packetHandler->write2ByteTxRx(portHandler, JOINT_ELBOW_ID, ADDR_SPEED, JOINT_ELBOW_SPEED, &dxl_error);
    checkCommResult(dxl_comm_result, packetHandler, dxl_error);

    dxl_comm_result = packetHandler->write2ByteTxRx(portHandler, JOINT_PADDLE_ID, ADDR_SPEED, JOINT_PADDLE_SPEED, &dxl_error);
    checkCommResult(dxl_comm_result, packetHandler, dxl_error);
    ROS_INFO("Initialized motor speed \n");

    // Change PID controls to allow incremental moves
    dxl_comm_result = packetHandler->write1ByteTxRx(portHandler, JOINT_PAN_ID, ADDR_CCW_COMPLIANCE_SLOPE, JOINT_PAN_CCW_COMPLIANCE_SLOPE, &dxl_error);
    checkCommResult(dxl_comm_result, packetHandler, dxl_error);

    dxl_comm_result = packetHandler->write1ByteTxRx(portHandler, JOINT_TILT_ID, ADDR_CCW_COMPLIANCE_SLOPE, JOINT_TILT_CCW_COMPLIANCE_SLOPE, &dxl_error);
    checkCommResult(dxl_comm_result, packetHandler, dxl_error);

    dxl_comm_result = packetHandler->write1ByteTxRx(portHandler, JOINT_ELBOW_ID, ADDR_CCW_COMPLIANCE_SLOPE, JOINT_ELBOW_CCW_COMPLIANCE_SLOPE, &dxl_error);
    checkCommResult(dxl_comm_result, packetHandler, dxl_error);

    dxl_comm_result = packetHandler->write1ByteTxRx(portHandler, JOINT_PADDLE_ID, ADDR_CCW_COMPLIANCE_SLOPE, JOINT_PADDLE_CCW_COMPLIANCE_SLOPE, &dxl_error);
    checkCommResult(dxl_comm_result, packetHandler, dxl_error);
    ROS_INFO("Initialized CCW Compliance Slope \n");

    dxl_comm_result = packetHandler->write1ByteTxRx(portHandler, JOINT_PAN_ID, ADDR_CW_COMPLIANCE_SLOPE, JOINT_PAN_CW_COMPLIANCE_SLOPE, &dxl_error);
    checkCommResult(dxl_comm_result, packetHandler, dxl_error);

    dxl_comm_result = packetHandler->write1ByteTxRx(portHandler, JOINT_TILT_ID, ADDR_CW_COMPLIANCE_SLOPE, JOINT_TILT_CW_COMPLIANCE_SLOPE, &dxl_error);
    checkCommResult(dxl_comm_result, packetHandler, dxl_error);

    dxl_comm_result = packetHandler->write1ByteTxRx(portHandler, JOINT_ELBOW_ID, ADDR_CW_COMPLIANCE_SLOPE, JOINT_ELBOW_CW_COMPLIANCE_SLOPE, &dxl_error);
    checkCommResult(dxl_comm_result, packetHandler, dxl_error);

    dxl_comm_result = packetHandler->write1ByteTxRx(portHandler, JOINT_PADDLE_ID, ADDR_CW_COMPLIANCE_SLOPE, JOINT_PADDLE_CW_COMPLIANCE_SLOPE, &dxl_error);
    checkCommResult(dxl_comm_result, packetHandler, dxl_error);
    ROS_INFO("Initialized CW Compliance Slope \n");

    //subcribe to joint_goal topic to get goal_pos
    ros::Subscriber arm_sub = n.subscribe("arm_goal", 1000, updateGoalArm);
    ros::Subscriber wristsub = n.subscribe("wrist_goal", 1000, updateGoalWrist);
    // publish the present position of motors
    ros::Publisher chatter_pub = n.advertise<pongbot::JointGoal>("joint_pos", 1000);

    int count = 0;
    ros::Rate r(100.0);
    while(n.ok()){
        // Read and store joint positions
        getJointPos(packetHandler, portHandler, dxl_comm_result, dxl_error);

        pongbot::JointGoal msg;

        msg.joints.push_back(joint_pos[0]);
        msg.joints.push_back(joint_pos[1]);
        msg.joints.push_back(joint_pos[2]);
        msg.joints.push_back(joint_pos[3]);

        chatter_pub.publish(msg);

        // Writing the goal position of the entire arm
        setJointPos(packetHandler, portHandler, dxl_comm_result, dxl_error);

        count++;
        ros::spinOnce();
        r.sleep();
    }
    // Close port
    portHandler->closePort();
    return 0;
}

/**
 * @brief Function to check the dynamixel comm result
 * @param dxl_comm_result, *packetHandler, dxl_error
 * */
void checkCommResult(int dxl_comm_result, dynamixel::PacketHandler *packetHandler, uint8_t dxl_error)
{
    if (dxl_comm_result != COMM_SUCCESS)
    {
        ROS_WARN(packetHandler->getTxRxResult(dxl_comm_result));
    }
    else if (dxl_error != 0)
    {
        ROS_WARN(packetHandler->getRxPacketError(dxl_error));
    }
}

/** Callback function for getting the goal position from subscribed topic
 * */
void updateGoalArm(const pongbot::JointGoal::ConstPtr& msg){
    //read for all except wrist motor
    for (size_t i=0; i<NUM_JOINTS-1; i++)
        goal_pos[i] = msg->joints.at(i);
}

/** Callback function for getting the goal wrist position from subscribed topic
 * */
void updateGoalWrist(const pongbot::WristGoal::ConstPtr& msg){
    wrist_goal = msg->wrist_goal;
}

/** Reads the position of all the joints and puts them into joint_pos[]
 * */
void getJointPos(dynamixel::PacketHandler* packetHandler, dynamixel::PortHandler* portHandler, int dxl_comm_result, uint8_t dxl_error)
{
    dxl_comm_result = packetHandler->read4ByteTxRx(portHandler, JOINT_PAN_ID, ADDR_PRESENT_POSITION, (uint32_t*)&joint_pos[0], &dxl_error);
    checkCommResult(dxl_comm_result, packetHandler, dxl_error);

    dxl_comm_result = packetHandler->read4ByteTxRx(portHandler, JOINT_TILT_ID, ADDR_PRESENT_POSITION, (uint32_t*)&joint_pos[1], &dxl_error);
    checkCommResult(dxl_comm_result, packetHandler, dxl_error);

    dxl_comm_result = packetHandler->read4ByteTxRx(portHandler, JOINT_ELBOW_ID, ADDR_PRESENT_POSITION, (uint32_t*)&joint_pos[2], &dxl_error);
    checkCommResult(dxl_comm_result, packetHandler, dxl_error);

    dxl_comm_result = packetHandler->read4ByteTxRx(portHandler, JOINT_PADDLE_ID, ADDR_PRESENT_POSITION, (uint32_t*)&joint_pos[3], &dxl_error);
    checkCommResult(dxl_comm_result, packetHandler, dxl_error);
}

/** Write out goal positions for each joint
 * */
void setJointPos(dynamixel::PacketHandler* packetHandler, dynamixel::PortHandler* portHandler, int dxl_comm_result, uint8_t dxl_error)
{
    dxl_comm_result = packetHandler->write2ByteTxRx(portHandler, JOINT_PAN_ID, ADDR_GOAL_POSITION, goal_pos[0], &dxl_error);
    checkCommResult(dxl_comm_result, packetHandler, dxl_error);

    dxl_comm_result = packetHandler->write2ByteTxRx(portHandler, JOINT_TILT_ID, ADDR_GOAL_POSITION, goal_pos[1], &dxl_error);
    checkCommResult(dxl_comm_result, packetHandler, dxl_error);

    dxl_comm_result = packetHandler->write2ByteTxRx(portHandler, JOINT_ELBOW_ID, ADDR_GOAL_POSITION, goal_pos[2], &dxl_error);
    checkCommResult(dxl_comm_result, packetHandler, dxl_error);

    dxl_comm_result = packetHandler->write2ByteTxRx(portHandler, JOINT_PADDLE_ID, ADDR_GOAL_POSITION, wrist_goal, &dxl_error);
    checkCommResult(dxl_comm_result, packetHandler, dxl_error);
}

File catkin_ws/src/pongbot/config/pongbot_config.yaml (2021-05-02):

# linux port and AX-12A baud rate
usb_port: "/dev/ttyUSB0"
dxl_baud_rate: 1000000

# control table addresses
addr_torque_enable: 24
addr_goal_position: 30
addr_present_position: 36
addr_speed: 32
addr_cw_compliance_slope: 28
addr_ccw_compliance_slope: 29

# AX-12A min max
dxl_minimum_position_value: 0
dxl_maximum_position_value: 1023

# Protocol version
protocol_version: 1.0

# Set the dynamixel id for various joints
joint_pan:
  ID: 1
  zero_config: 512
  speed: 200
  cw_compliance_slope: 32
  ccw_compliance_slope: 32
  min: 0
  max: 1023
joint_tilt:
  ID: 2
  zero_config: 819
  speed: 200
  cw_compliance_slope: 144
  ccw_compliance_slope: 144
  min: 200
  max: 820
joint_elbow:
  ID: 3
  zero_config: 819
  speed: 200
  cw_compliance_slope: 64
  ccw_compliance_slope: 64
  min: 300
  max: 923
joint_paddle:
  ID: 4
  zero_config: 512
  speed: 200
  cw_compliance_slope: 32
  ccw_compliance_slope: 32
  min: 0
  max: 1023

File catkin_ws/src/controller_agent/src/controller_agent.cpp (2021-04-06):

#include <ros/ros.h>
#include <ros/console.h>
#include <dynamixel_sdk.h>

#include <stdlib.h>
#include <stdio.h>
#include <string>

#define TORQUE_ENABLE   1
#define TORQUE_DISABLE  0

int main(int argc, char** argv)
{
    // init node
    ros::init(argc, argv, "controller_agent");

    ros::NodeHandle n;

    // Get all parameters from the yaml config file
    std::string DEVICENAME;
    int DXL_MINIMUM_POSITION_VALUE, DXL_MAXIMUM_POSITION_VALUE, BAUDRATE;
    float PROTOCOL_VERSION;
    int ADDR_TORQUE_ENABLE, ADDR_GOAL_POSITION, ADDR_PRESENT_POSITION;
    int AGENT_PAN_ID, AGENT_TILT_ID, CONTROL_PAN_ID, CONTROL_TILT_ID;

    n.getParam("usb_port", DEVICENAME);
    n.getParam("dxl_minimum_position_value", DXL_MINIMUM_POSITION_VALUE);
    n.getParam("dxl_maximum_position_value", DXL_MAXIMUM_POSITION_VALUE);
    n.getParam("dxl_baud_rate", BAUDRATE);
    n.getParam("protocol_version", PROTOCOL_VERSION);
    n.getParam("addr_torque_enable", ADDR_TORQUE_ENABLE);
    n.getParam("addr_goal_position", ADDR_GOAL_POSITION);
    n.getParam("addr_present_position", ADDR_PRESENT_POSITION);
    n.getParam("agent_pan/ID", AGENT_PAN_ID);
    n.getParam("agent_tilt/ID", AGENT_TILT_ID);
    n.getParam("control_pan/ID", CONTROL_PAN_ID);
    n.getParam("control_tilt/ID", CONTROL_TILT_ID);

    // Initialize PortHandler instance
    // Set the port path
    // Get methods and members of PortHandlerLinux or PortHandlerWindows
    dynamixel::PortHandler *portHandler = dynamixel::PortHandler::getPortHandler(DEVICENAME.c_str());

    // Initialize PacketHandler instance
    // Set the protocol version
    // Get methods and members of Protocol1PacketHandler or Protocol2PacketHandler
    dynamixel::PacketHandler *packetHandler = dynamixel::PacketHandler::getPacketHandler(PROTOCOL_VERSION);

    int dxl_comm_result = COMM_TX_FAIL;             // Communication result

    uint8_t dxl_error = 0;                          // Dynamixel error

    // present positions
    int32_t agent_pan_present_position = 0, agent_tilt_present_position = 0;
    int32_t control_pan_present_position = 0, control_tilt_present_position = 0;

    // Open port
    if (portHandler->openPort())
    {
        ROS_INFO("Succeeded to open the port!\n");
    }
    else
    {
        ROS_ERROR("Failed to open the port!\n");
        return 0;
    }

    // Set port baudrate
    if (portHandler->setBaudRate(BAUDRATE))
    {
        ROS_INFO("Succeeded to change the baudrate!\n");
    }
    else
    {
        ROS_ERROR("Failed to change the baudrate!\n");
        return 0;
    }

    // initialize and connect to each motor
    dxl_comm_result = packetHandler->write1ByteTxRx(portHandler, AGENT_PAN_ID, ADDR_TORQUE_ENABLE, TORQUE_ENABLE, &dxl_error);
    if (dxl_comm_result != COMM_SUCCESS)
    {
        ROS_WARN(packetHandler->getTxRxResult(dxl_comm_result));
    }
    else if (dxl_error != 0)
    {
        ROS_WARN(packetHandler->getRxPacketError(dxl_error));
    }
    else
    {
        ROS_INFO("Agent Pan motor has been successfully connected \n");
    } 

    dxl_comm_result = packetHandler->write1ByteTxRx(portHandler, AGENT_TILT_ID, ADDR_TORQUE_ENABLE, TORQUE_ENABLE, &dxl_error);
    if (dxl_comm_result != COMM_SUCCESS)
    {
        ROS_WARN(packetHandler->getTxRxResult(dxl_comm_result));
    }
    else if (dxl_error != 0)
    {
        ROS_WARN(packetHandler->getRxPacketError(dxl_error));
    }
    else
    {
        ROS_INFO("Agent Tilt motor has been successfully connected \n");
    } 

    dxl_comm_result = packetHandler->write1ByteTxRx(portHandler, CONTROL_PAN_ID, ADDR_TORQUE_ENABLE, TORQUE_DISABLE, &dxl_error);
    if (dxl_comm_result != COMM_SUCCESS)
    {
        ROS_WARN(packetHandler->getTxRxResult(dxl_comm_result));
    }
    else if (dxl_error != 0)
    {
        ROS_WARN(packetHandler->getRxPacketError(dxl_error));
    }
    else
    {
        ROS_INFO("Controller Pan motor has been successfully connected \n");
    } 

    dxl_comm_result = packetHandler->write1ByteTxRx(portHandler, CONTROL_TILT_ID, ADDR_TORQUE_ENABLE, TORQUE_DISABLE, &dxl_error);
    if (dxl_comm_result != COMM_SUCCESS)
    {
        ROS_WARN(packetHandler->getTxRxResult(dxl_comm_result));
    }
    else if (dxl_error != 0)
    {
        ROS_WARN(packetHandler->getRxPacketError(dxl_error));
    }
    else
    {
        ROS_INFO("Controller Tilt motor has been successfully connected \n");
    } 

    int count = 0;
    ros::Rate r(1.0);
    while(n.ok()){
        do
        {
            // Read control pan motor present position
            dxl_comm_result = packetHandler->read4ByteTxRx(portHandler, CONTROL_PAN_ID, ADDR_PRESENT_POSITION, (uint32_t*)&control_pan_present_position, &dxl_error);
            if (dxl_comm_result != COMM_SUCCESS)
            {
                ROS_WARN(packetHandler->getTxRxResult(dxl_comm_result));
            }
            else if (dxl_error != 0)
            {
                ROS_WARN(packetHandler->getRxPacketError(dxl_error));
            }

            // Read Control tilt motor present position
            dxl_comm_result = packetHandler->read4ByteTxRx(portHandler, CONTROL_TILT_ID, ADDR_PRESENT_POSITION, (uint32_t*)&control_tilt_present_position, &dxl_error);
            if (dxl_comm_result != COMM_SUCCESS)
            {
                ROS_WARN(packetHandler->getTxRxResult(dxl_comm_result));
            }
            else if (dxl_error != 0)
            {
                ROS_WARN(packetHandler->getRxPacketError(dxl_error));
            }

            // Read Agent Pan motor present position
            dxl_comm_result = packetHandler->read4ByteTxRx(portHandler, AGENT_PAN_ID, ADDR_PRESENT_POSITION, (uint32_t*)&agent_pan_present_position, &dxl_error);
            if (dxl_comm_result != COMM_SUCCESS)
            {
                ROS_WARN(packetHandler->getTxRxResult(dxl_comm_result));
            }
            else if (dxl_error != 0)
            {
                ROS_WARN(packetHandler->getRxPacketError(dxl_error));
            }

            // Read Agent tilt motor present position
            dxl_comm_result = packetHandler->read4ByteTxRx(portHandler, AGENT_TILT_ID, ADDR_PRESENT_POSITION, (uint32_t*)&agent_tilt_present_position, &dxl_error);
            if (dxl_comm_result != COMM_SUCCESS)
            {
                ROS_WARN(packetHandler->getTxRxResult(dxl_comm_result));
            }
            else if (dxl_error != 0)
            {
                ROS_WARN(packetHandler->getRxPacketError(dxl_error));
            }

            // Write agent pan goal position
            dxl_comm_result = packetHandler->write4ByteTxRx(portHandler, AGENT_PAN_ID, ADDR_GOAL_POSITION, control_pan_present_position, &dxl_error);
            if (dxl_comm_result != COMM_SUCCESS)
            {
                ROS_WARN(packetHandler->getTxRxResult(dxl_comm_result));
            }
            else if (dxl_error != 0)
            {
                ROS_WARN(packetHandler->getRxPacketError(dxl_error));
            }
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

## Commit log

2021-03-31 Added male link connector model
    [Male_Link_Connector-Body.stl, Male_Link_Connector.FCStd]
2021-03-31 Male Link Connector Revision
    [Male_Link_Connector-Body.stl, Male_Link_Connector.FCStd]
2021-03-31 Male Link Connector Revision2
    [Male_Link_Connector-Body.stl, Male_Link_Connector.FCStd]
2021-03-31 Link Prototype
    [Link_prototype-Body.stl, Link_prototype.FCStd]
2021-04-01 Male Link Connector redesign
    [Male_Link_Connector-Body.stl, Male_Link_Connector.FCStd]
2021-04-01 Link Connector
    [Link_Connector-Body.stl]
2021-04-01 Link Connector revision
    [Link_Connector-Body.stl]
2021-04-01 Found WebmasterZero's models on thingiverse...
    [Male_Link_Connector.FCStd, base_legs_arbotix_m.stl, base_turn_table.stl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]
2021-04-05 init catkin_ws and controller_agent pkg
    [AX-12A.dwg]
2021-04-07 Added base board cad
    [base1-Body.stl, base1.FCStd]
2021-04-08 base revision
    [base1-Body.stl, base1.FCStd]
2021-04-08 design of second level of base
    [base2-BodyPocket002.stl, base2.FCStd]
2021-04-10 center hole of base2
    [base2-Body.stl, base2.FCStd]
2021-04-10 created rim of 3rd floor base
    [base3_rim-Body.stl, base3_rim.FCStd]
2021-04-10 created turntable
    [base3_turntable-Body.stl, base3_turntable.FCStd]
2021-04-10 adjusted screw hole size
    [base2-Body.stl, base2.FCStd, base3_turntable-Body.stl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]
2021-04-16 Added link1 frame
    [Male_Link1_Panel-Body.stl, Male_Link1_Panel.FCStd]
2021-04-16 Added link1 frame revision
    [Male_Link1_Panel-Body.stl, Male_Link1_Panel.FCStd]
2021-04-17 Added female link backplate
    [Female_Link1_backPanel-Body.stl, Female_Link1_backPanel.FCStd]
2021-04-17 female link backplate revision
    [Female_Link1_backPanel-Body.stl, Female_Link1_backPanel.FCStd, Link_Connector-Body.stl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]
2021-04-17 male link panel revision
    [Male_Link1_Panel-Body.stl, Male_Link1_Panel.FCStd]
2021-04-17 female link frontplate
    [Female_Link1_backPanel.FCStd, Female_Link1_frontPanel-Body.stl, Female_Link1_frontPanel.FCStd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]
2021-04-17 female link frontplate revision
    [Female_Link1_frontPanel-Body.stl, Female_Link1_frontPanel.FCStd]
2021-04-18 Added second link
    [Link2_sidepanel-Body.stl, Link2_sidepanel.FCStd]
2021-04-18 Added second link revision
    [Link2_sidepanel-Body.stl, Link2_sidepanel.FCStd]
2021-04-18 Added paddle
    [paddle-Body.stl, paddle.FCStd]
2021-04-18 Added paddle holder
    [paddle_holder-Body.stl, paddle_holder.FCStd]
2021-04-18 Paddle revision
    [paddle-Body.stl, paddle.FCStd]
2021-04-18 Added paddle holder revision
    [paddle_holder-Body.stl, paddle_holder.FCStd]
2021-04-19 Organized folder
    [AX-12A.dwg, Female_Link1_frontPanel.FCStd, Link_prototype.FCStd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]
2021-04-19 Base1 revision for steel plate
    [base1-Body.stl, base1.FCStd]
2021-04-21 Base2 revision, increased thickness
    [base2-Body.stl, base2.FCStd]
2021-04-21 Base2 revision, added extra holes
    [base2-Body.stl, base2.FCStd]
2021-04-21 Turntable revision, increased thickness
    [base3_turntable-Body.stl, base3_turntable.FCStd]
2021-04-21 Turntable revision, spaced slot
    [base3_turntable-Body.stl, base3_turntable.FCStd]
2021-04-21 Turntable spacer added
    [turntable_spacer-Body.stl, turntable_spacer.FCStd]
2021-04-21 changed slot space of base2 and turntable
    [base2-Body.stl, base2.FCStd, base3_turntable-Body.stl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]
2021-04-22 added stop rod for paddle
    [paddle_holder.FCStd, stop_rod-Body.stl, stop_rod.FCStd]
2021-04-22 added turntable support
    [turntable_support-Fusion.stl, turntable_support.FCStd]
2021-04-23 Turntable support revision
    [turntable_support-Fusion.stl, turntable_support.FCStd]
2021-04-24 jittery controller for arm to move to zero config
    [pongbot_demo.cpp]
2021-04-29 driver node that subscribes to topic to get goal
2021-04-29 separated wrist from arm in publishers
2021-04-30 very buggy forward kinematics code
2021-04-30 Will now dynamically display forward kinematics as robot operates
2021-05-02 fixed bugs and now dummy publisher works in radian
    [pongbot_config.yaml]
2021-05-03 Initialized Inverse Kinematics node/msg
2021-05-03 naive inverse kinematics
2021-05-03 fix inverse kinematics
2021-05-03 added a wrist driver node
2021-05-27 added urdf visualization launch file
2021-05-27 added stl files for urdf mesh
    [Female_Link1_backPanel-Body.stl, Female_Link1_frontPanel-Body.stl, Link2_sidepanel-Body.stl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]
2021-05-27 urdf file describing pongbot!
    [pongbot.urdf]
2021-05-27 rviz config for urdf
2021-05-28 updated readme and added urdf pic
2021-05-29 added components to allow gazebo simulation
    [pongbot.urdf]
